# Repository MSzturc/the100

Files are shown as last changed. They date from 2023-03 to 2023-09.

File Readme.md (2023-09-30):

<p>

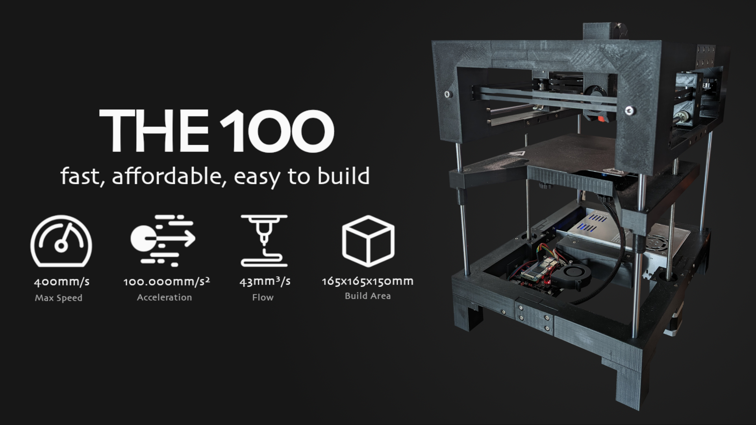
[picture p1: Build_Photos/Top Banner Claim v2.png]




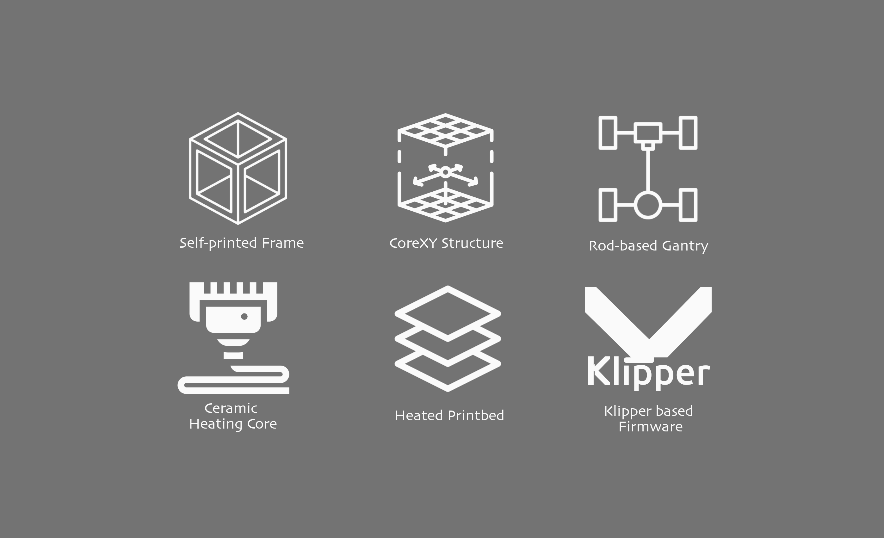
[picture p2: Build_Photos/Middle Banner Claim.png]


<a href="https://www.youtube.com/watch?v=oDKtKg4UfsU" > 
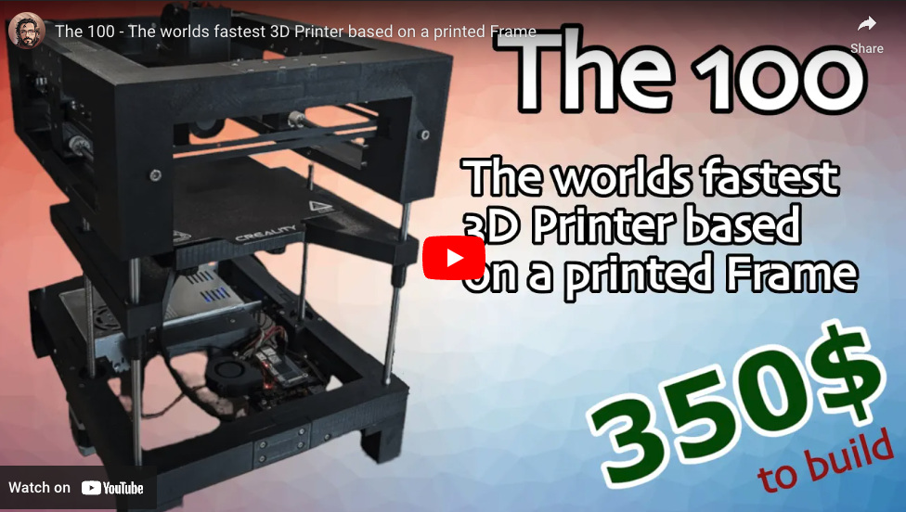
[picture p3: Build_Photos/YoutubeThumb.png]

</a>

</p>

# THE 100, the fastest 3D Printer based on a printed frame.

- It does Speedboat in less than 6 minutes and is capable of doing high quality prints in **1/10th** of the time a Ender 3 would need.
- By the time releasing, The 100 is at the 26th rank of the [leaderboard](https://docs.google.com/spreadsheets/d/1lFiJi-X3Xm3hh3I9Ty9dfACMiBWxHFAOUeiU1km9m6I/edit#gid=106736391) of the fastest printers in the world and it's the fastest one that uses a 3d printed frame.
- And the best thing, this printer **100% open source**. Which means if you like this printer and you  like to build one by own, you find all resources needed to do this in this repository

## Links
- [Bill of Material](https://docs.google.com/spreadsheets/d/1e5dhm4ck-dtci_GDkMuuwxgp788YJ5hdL6JvRKvF1Zc/edit?usp=sharing)
- [Join our Discord Server](https://discord.gg/fW7BcUErgZ)
- [Support this Project on Patreon](https://www.patreon.com/The100)
- [Grad the CAD files](https://www.printables.com/model/572689-the-100-the-fastest-3d-printer-based-on-a-printed-)
- [View the Assembly Guide](https://www.youtube.com/playlist?list=PLM01o_dfwbDcKYB-9yV0vLs5k0CrHUv0W)
- [Follow the Development](https://hackaday.io/project/190348-the-100-the-fastest-3d-printer)
- [Our Community on Facebook](https://www.facebook.com/groups/181335024786568)
- [Printers build by the Community](https://www.youtube.com/playlist?list=PLM01o_dfwbDfZ-m0T0c431_AJRJ2Jxip3)

## Print Settings

To print the STL files, a 3D printer with a print bed of at least 230x230mm is required.
I've printed all parts out of PLA. If you plan to print ABS/ASA on the printer i would suggest to print the print bed out of a more temprature resistant material.

For all STL Parts **exept the print bed** i've used the following settings:

- 0.25 Layer height
- 0.5 Line width
- 3 Top layers
- 3 Bottom layers
- 3 Walls
- 25% Infill
- Grid Infill Pattern

**For the print bed:**
- 30% Infill

The infill of the print bed needs to be slightly higher to move the center of gravity to where the lead screws are attached. This is needed to stop binding on the Z-Axis.

## Specifications

- Printing Technology: FDM
- Build Volume: 165x165x150mm
- Maximum Printing Speed: 400mm/s
- Maximum Acceleration: 100.000mm/s²
- Layer Height: 0.1-0.35mm
- Extruder: BMG Bowden Extruder
- Filament Diameter: 1.75mm
- Nozzle Diameter: 0.4 (swappable)
- Maximum Nozzle Temperature: 300°C
- Maximum Heatbed Temperature: 110°C
- Leveling Mode: manual
- File Transfer: USB Drive, WIFI
- Rated Power: 350W
- Supported Filaments: PLA, PETG

## Builds by the Community

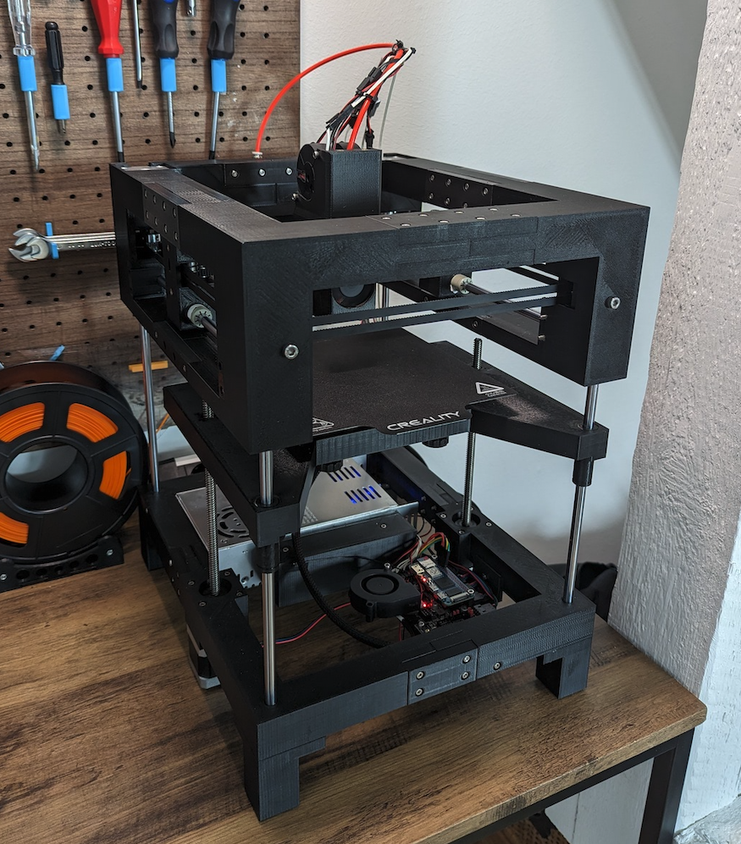
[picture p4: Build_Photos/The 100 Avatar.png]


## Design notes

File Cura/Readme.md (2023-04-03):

1. Add a new Printer in Cura:

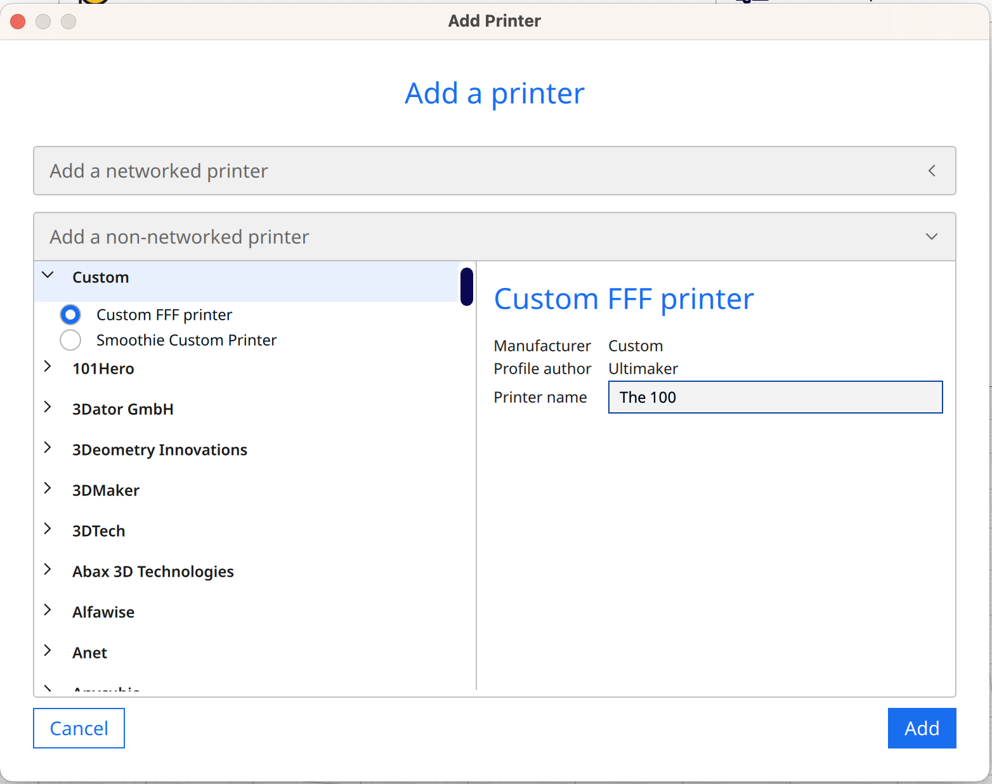
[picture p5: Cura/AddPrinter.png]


2. With following Printer Settings:

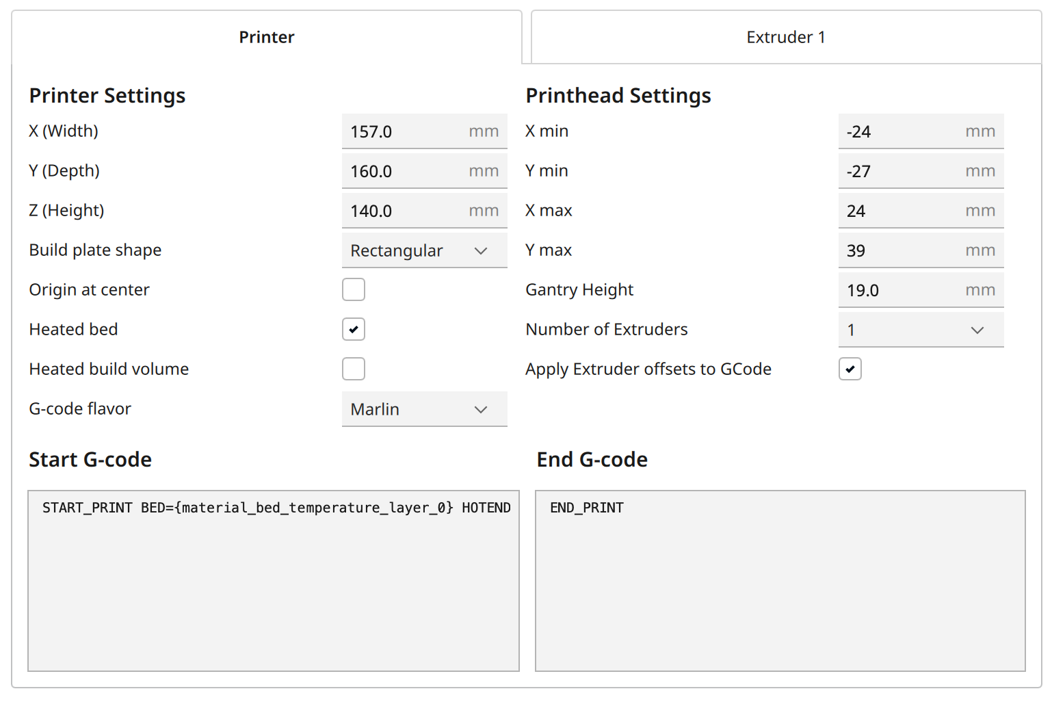
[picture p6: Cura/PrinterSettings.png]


Use as start GCODE:

> START_PRINT BED={material_bed_temperature_layer_0} HOTEND={material_print_temperature_layer_0}

3. and following Extruder Settings:

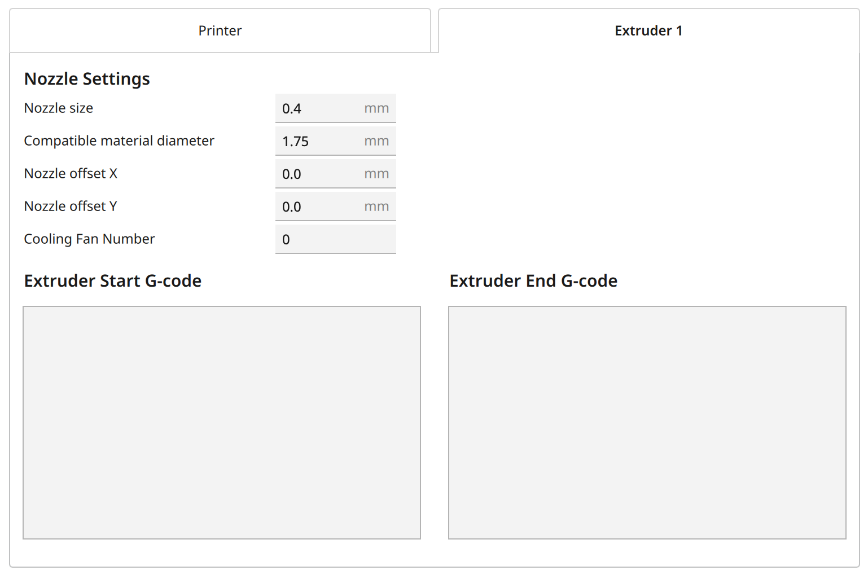
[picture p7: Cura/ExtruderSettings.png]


4. Import profiles at **Preferences->Configure Cura->Profiles** by pressing the Import button
5. Install the Moonraker plugin to communicate with the printer through WIFI. You have to add the Ip Address of the printer in the Moonraker Settings.

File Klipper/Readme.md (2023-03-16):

This config is for the BIGTREETECH SKR Pico.
It uses Klipper v0.11.0.116  with mainsail 2.4.1 and moonraker 0.7.1

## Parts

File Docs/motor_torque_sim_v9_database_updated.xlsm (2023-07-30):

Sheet: UI
 |  |  |  |  |  |  |  |  |  |  |  |  |  |  |  |  | Stepper Torque, 24V, 20T, 20k, 500g, 50W |  |  |  |  |  |  |  |  |  |  |  |  |  |  |  |  | Stepper Power, 24V, 20T, 20k, 500g, 50W
 | Input Voltage | 24 | Volts |  | 24V, 20T, 20k, 500g, 50W |  |  |  |  |  |  |  |  |  |  | mm/s | Cloudray-17CS05A-180E | LDO-42STH48-2504AC | Wantai-42BYGHW811 | G-Penny-42HS4825A4 | RATTM-17HS3410 | LDO-42STH48-2804AC | YunTaiKe-42CM02 | Motech-MT-1704HSM168RE | LDO-42STH48-2504MAC(F) | Moons-MS17HA2P4200 | 0 | 0 | 0 | 0 | 0 | 0 | Torque Required | mm/s | Cloudray-17CS05A-180E | LDO-42STH48-2504AC | Wantai-42BYGHW811 | G-Penny-42HS4825A4 | RATTM-17HS3410 | LDO-42STH48-2804AC | YunTaiKe-42CM02 | Motech-MT-1704HSM168RE | LDO-42STH48-2504MAC(F) | Moons-MS17HA2P4200 | 0 | 0 | 0 | 0 | 0 | 0
 | Max Drive Current | 0.8 | Amps |  |  |  |  |  |  |  |  |  |  |  | 0 | 0 | 13.8 | 9.8 | 8.5 | 9.2 | 8.3 | 5.8 | 6.4 | 12.4 | 7.5 | 9.2 | #VALUE! | #VALUE! | #VALUE! | #VALUE! | #VALUE! | #VALUE! | 6.4 | 0 | 1.5 | 0.8 | 0.8 | 1.0 | 0.8 | 0.4 | 0.9 | 1.1 | 0.8 | 0.7 | #VALUE! | #VALUE! | #VALUE! | #VALUE! | #VALUE! | #VALUE!
 | Max Drive Percent | 100% |  |  |  |  |  |  |  |  |  |  |  |  | 0.5 | 20 | 13.8 | 9.8 | 8.5 | 9.2 | 8.3 | 5.8 | 6.4 | 12.4 | 7.5 | 9.2 | #VALUE! | #VALUE! | #VALUE! | #VALUE! | #VALUE! | #VALUE! | 6.4 | 20 | 2.0 | 1.2 | 1.1 | 1.4 | 1.1 | 0.7 | 1.1 | 1.5 | 1.1 | 1.0 | #VALUE! | #VALUE! | #VALUE! | #VALUE! | #VALUE! | #VALUE!
 | Max Power | 50 | W |  |  |  |  |  |  |  |  |  |  |  | 1 | 40 | 13.8 | 9.8 | 8.5 | 9.2 | 8.3 | 5.8 | 6.4 | 12.4 | 7.5 | 9.2 | #VALUE! | #VALUE! | #VALUE! | #VALUE! | #VALUE! | #VALUE! | 6.4 | 40 | 2.6 | 1.6 | 1.5 | 1.7 | 1.4 | 1.0 | 1.4 | 2.0 | 1.4 | 1.4 | #VALUE! | #VALUE! | #VALUE! | #VALUE! | #VALUE! | #VALUE!
 | Pulley Size | 20 | Teeth | 6.366197724 | mm |  |  |  |  |  |  |  |  |  | 1.5 | 60 | 13.8 | 9.8 | 8.5 | 9.2 | 8.3 | 5.8 | 6.4 | 12.4 | 7.5 | 9.2 | #VALUE! | #VALUE! | #VALUE! | #VALUE! | #VALUE! | #VALUE! | 6.4 | 60 | 3.1 | 1.9 | 1.8 | 2.1 | 1.6 | 1.2 | 1.6 | 2.4 | 1.7 | 1.7 | #VALUE! | #VALUE! | #VALUE! | #VALUE! | #VALUE! | #VALUE!
 | Gear Ratio | 1 |  |  |  |  |  |  |  |  |  |  |  |  | 2 | 80 | 13.8 | 9.8 | 8.5 | 9.2 | 8.3 | 5.8 | 6.4 | 12.4 | 7.5 | 9.2 | #VALUE! | #VALUE! | #VALUE! | #VALUE! | #VALUE! | #VALUE! | 6.4 | 80 | 3.6 | 2.3 | 2.1 | 2.4 | 1.9 | 1.5 | 1.8 | 2.9 | 2.0 | 2.1 | #VALUE! | #VALUE! | #VALUE! | #VALUE! | #VALUE! | #VALUE!
 |  |  |  |  |  |  |  |  |  |  |  |  |  |  | 2.5 | 100 | 13.8 | 9.8 | 8.5 | 9.2 | 8.3 | 5.8 | 6.4 | 12.4 | 7.5 | 9.2 | #VALUE! | #VALUE! | #VALUE! | #VALUE! | #VALUE! | #VALUE! | 6.4 | 100 | 4.1 | 2.7 | 2.5 | 2.8 | 2.2 | 1.8 | 2.1 | 3.3 | 2.4 | 2.4 | #VALUE! | #VALUE! | #VALUE! | #VALUE! | #VALUE! | #VALUE!
 | Acceleration | 20000 | mm/s^2 |  |  |  |  |  |  |  |  |  |  |  | 3 | 120 | 13.8 | 9.8 | 8.5 | 9.2 | 8.3 | 5.8 | 6.4 | 12.4 | 7.5 | 9.2 | #VALUE! | #VALUE! | #VALUE! | #VALUE! | #VALUE! | #VALUE! | 6.4 | 120 | 4.6 | 3.1 | 2.8 | 3.2 | 2.5 | 2.0 | 2.3 | 3.8 | 2.7 | 2.8 | #VALUE! | #VALUE! | #VALUE! | #VALUE! | #VALUE! | #VALUE!
 | Toolhead + Y axis mass | 500 | g |  |  |  |  |  |  |  |  |  |  |  | 3.5 | 140 | 13.8 | 9.8 | 8.5 | 9.2 | 8.3 | 5.8 | 6.4 | 12.4 | 7.5 | 9.2 | #VALUE! | #VALUE! | #VALUE! | #VALUE! | #VALUE! | #VALUE! | 6.4 | 140 | 5.1 | 3.5 | 3.1 | 3.5 | 2.8 | 2.3 | 2.6 | 4.2 | 3.0 | 3.1 | #VALUE! | #VALUE! | #VALUE! | #VALUE! | #VALUE! | #VALUE!
 | Torque Required | 6.37 | N-cm | 0.06366197724 |  |  |  |  |  |  |  |  |  |  | 4 | 160 | 13.8 | 9.8 | 8.5 | 9.2 | 8.3 | 5.8 | 6.4 | 12.4 | 7.5 | 9.2 | #VALUE! | #VALUE! | #VALUE! | #VALUE! | #VALUE! | #VALUE! | 6.4 | 160 | 5.6 | 3.9 | 3.5 | 3.9 | 3.1 | 2.6 | 2.8 | 4.7 | 3.3 | 3.4 | #VALUE! | #VALUE! | #VALUE! | #VALUE! | #VALUE! | #VALUE!
 |  |  |  |  |  |  |  |  |  |  |  |  |  |  | 4.5 | 180 | 13.8 | 9.8 | 8.5 | 9.2 | 8.3 | 5.8 | 6.4 | 12.4 | 7.5 | 9.2 | #VALUE! | #VALUE! | #VALUE! | #VALUE! | #VALUE! | #VALUE! | 6.4 | 180 | 6.2 | 4.3 | 3.8 | 4.2 | 3.4 | 2.8 | 3.0 | 5.2 | 3.6 | 3.8 | #VALUE! | #VALUE! | #VALUE! | #VALUE! | #VALUE! | #VALUE!
 |  |  | NEMA | Body Length | Step Angle | Rated Current | Torque | Inductance | Resistance | Rotor Inertia | Max Current at Specified Power | Drive Current | Torque Rotor | Power at drive current | 5 | 200 | 13.8 | 9.8 | 8.5 | 9.2 | 8.3 | 5.8 | 6.4 | 12.4 | 7.5 | 9.2 | #VALUE! | #VALUE! | #VALUE! | #VALUE! | #VALUE! | #VALUE! | 6.4 | 200 | 6.7 | 4.7 | 4.1 | 4.6 | 3.7 | 3.1 | 3.3 | 5.6 | 4.0 | 4.1 | #VALUE! | #VALUE! | #VALUE! | #VALUE! | #VALUE! | #VALUE!
Motor 1 |  | Cloudray-17CS05A-180E | 17 | 48 | 1.8 | 1.8 | 52 | 5.8 | 2.4 | 82 | 3.23 | 0.80 | 2.58 | 3.072 | 5.5 | 220 | 13.8 | 9.8 | 8.5 | 9.2 | 8.3 | 5.8 | 6.4 | 12.4 | 7.5 | 9.2 | #VALUE! | #VALUE! | #VALUE! | #VALUE! | #VALUE! | #VALUE! | 6.4 | 220 | 7.2 | 5.1 | 4.5 | 4.9 | 4.0 | 3.4 | 3.5 | 6.1 | 4.3 | 4.5 | #VALUE! | #VALUE! | #VALUE! | #VALUE! | #VALUE! | #VALUE!
Motor 2 |  | LDO-42STH48-2504AC | 17 | 48 | 1.8 | 2.5 | 55 | 1.5 | 1.2 | 84.5 | 4.56 | 0.80 | 2.65 | 1.536 | 6 | 240 | 13.8 | 9.8 | 8.5 | 9.2 | 8.3 | 5.8 | 6.4 | 12.4 | 7.5 | 9.2 | #VALUE! | #VALUE! | #VALUE! | #VALUE! | #VALUE! | #VALUE! | 6.4 | 240 | 7.7 | 5.5 | 4.8 | 5.3 | 4.3 | 3.6 | 3.7 | 6.5 | 4.6 | 4.8 | #VALUE! | #VALUE! | #VALUE! | #VALUE! | #VALUE! | #VALUE!
Motor 3 |  | Wantai-42BYGHW811 | 17 | 48 | 1.8 | 2.5 | 47 | 1.8 | 1.25 | 68 | 4.47 | 0.80 | 2.14 | 1.6 | 6.5 | 260 | 13.8 | 9.8 | 8.5 | 9.2 | 8.3 | 5.8 | 6.4 | 12.4 | 7.5 | 9.2 | #VALUE! | #VALUE! | #VALUE! | #VALUE! | #VALUE! | #VALUE! | 6.4 | 260 | 8.2 | 5.9 | 5.1 | 5.6 | 4.6 | 3.9 | 4.0 | 7.0 | 4.9 | 5.2 | #VALUE! | #VALUE! | #VALUE! | #VALUE! | #VALUE! | #VALUE!
Motor 4 |  | G-Penny-42HS4825A4 | 17 | 48 | 1.8 | 2.5 | 50 | 1.8 | 1.6 | 68 | 3.95 | 0.80 | 2.14 | 2.048 | 7 | 280 | 13.8 | 9.8 | 8.5 | 9.2 | 8.3 | 5.8 | 6.4 | 12.4 | 7.5 | 9.2 | #VALUE! | #VALUE! | #VALUE! | #VALUE! | #VALUE! | #VALUE! | 6.4 | 280 | 8.7 | 6.2 | 5.5 | 6.0 | 4.9 | 4.2 | 4.2 | 7.4 | 5.2 | 5.5 | #VALUE! | #VALUE! | #VALUE! | #VALUE! | #VALUE! | #VALUE!
Motor 5 |  | RATTM-17HS3410 | 17 | 34 | 1.8 | 1.7 | 28 | 1.8 | 1.2 | 34 | 4.56 | 0.80 | 1.07 | 1.536 | 7.5 | 300 | 13.8 | 9.8 | 8.5 | 9.2 | 8.3 | 5.8 | 6.4 | 12.4 | 7.5 | 9.2 | #VALUE! | #VALUE! | #VALUE! | #VALUE! | #VALUE! | #VALUE! | 6.4 | 300 | 9.2 | 6.6 | 5.8 | 6.4 | 5.2 | 4.4 | 4.5 | 7.9 | 5.6 | 5.9 | #VALUE! | #VALUE! | #VALUE! | #VALUE! | #VALUE! | #VALUE!
Motor 6 |  | LDO-42STH48-2804AC | 17 | 48 | 1.8 | 2.8 | 42 | 0.6 | 0.7 | 84.5 | 5.98 | 0.80 | 2.65 | 0.896 | 8 | 320 | 13.8 | 9.8 | 8.5 | 9.2 | 8.3 | 5.8 | 6.4 | 12.4 | 7.5 | 9.2 | #VALUE! | #VALUE! | #VALUE! | #VALUE! | #VALUE! | #VALUE! | 6.4 | 320 | 9.8 | 7.0 | 6.1 | 6.7 | 5.5 | 4.7 | 4.7 | 8.4 | 5.9 | 6.2 | #VALUE! | #VALUE! | #VALUE! | #VALUE! | #VALUE! | #VALUE!
Motor 7 |  | YunTaiKe-42CM02 | 17 | 33 | 1.8 | 1.5 | 20 | 1.4 | 1.4 | 35 | 4.23 | 0.80 | 1.10 | 1.792 | 8.5 | 340 | 12.4 | 9.8 | 8.5 | 9.2 | 8.3 | 5.8 | 6.4 | 12.4 | 7.5 | 9.2 | #VALUE! | #VALUE! | #VALUE! | #VALUE! | #VALUE! | #VALUE! | 6.4 | 340 | 9.3 | 7.4 | 6.5 | 7.1 | 5.7 | 5.0 | 4.9 | 8.8 | 6.2 | 6.6 | #VALUE! | #VALUE! | #VALUE! | #VALUE! | #VALUE! | #VALUE!
Motor 8 |  | Motech-MT-1704HSM168RE | 17 | 48 | 0.9 | 1.68 | 43.12 | 2.8 | 1.65 | 68 | 3.89 | 0.80 | 2.14 |  | 9 | 360 | 11.0 | 9.8 | 8.5 | 9.2 | 8.3 | 5.8 | 6.4 | 12.1 | 7.5 | 9.2 | #VALUE! | #VALUE! | #VALUE! | #VALUE! | #VALUE! | #VALUE! | 6.4 | 360 | 8.7 | 7.8 | 6.8 | 7.4 | 6.0 | 5.2 | 5.2 | 9.1 | 6.5 | 6.9 | #VALUE! | #VALUE! | #VALUE! | #VALUE! | #VALUE! | #VALUE!
Motor 9 |  | LDO-42STH48-2504MAC(F) | 17 | 48 | 0.9 | 2.5 | 45 | 1.5 | 1.2 | 85 | 4.56 | 0.80 | 2.67 |  | 9.5 | 380 | 9.7 | 9.8 | 8.5 | 9.2 | 8.3 | 5.8 | 6.4 | 10.9 | 7.5 | 9.2 | #VALUE! | #VALUE! | #VALUE! | #VALUE! | #VALUE! | #VALUE! | 6.4 | 380 | 8.2 | 8.2 | 7.1 | 7.8 | 6.3 | 5.5 | 5.4 | 8.6 | 6.8 | 7.3 | #VALUE! | #VALUE! | #VALUE! | #VALUE! | #VALUE! | #VALUE!
Motor 10 |  | Moons-MS17HA2P4200 | 17 | 40 | 0.9 | 2 | 39 | 2.8 | 1.05 | 57 | 4.88 | 0.80 | 1.79 |  | 10 | 400 | 8.5 | 9.8 | 8.5 | 9.2 | 8.3 | 5.8 | 6.4 | 9.7 | 7.5 | 9.2 | #VALUE! | #VALUE! | #VALUE! | #VALUE! | #VALUE! | #VALUE! | 6.4 | 400 | 7.7 | 8.6 | 7.5 | 8.1 | 6.6 | 5.8 | 5.6 | 8.2 | 7.2 | 7.6 | #VALUE! | #VALUE! | #VALUE! | #VALUE! | #VALUE! | #VALUE!
Motor 11 |  |  | #N/A | #N/A | #N/A | #N/A | #N/A | #N/A | #N/A | #N/A | #N/A | #N/A | #N/A |  | 10.5 | 420 | 7.4 | 9.8 | 8.5 | 9.2 | 8.3 | 5.8 | 6.4 | 8.7 | 7.5 | 8.7 | #VALUE! | #VALUE! | #VALUE! | #VALUE! | #VALUE! | #VALUE! | 6.4 | 420 | 7.2 | 9.0 | 7.8 | 8.5 | 6.9 | 6.0 | 5.9 | 7.7 | 7.5 | 7.6 | #VALUE! | #VALUE! | #VALUE! | #VALUE! | #VALUE! | #VALUE!
Motor 12 |  |  | #N/A | #N/A | #N/A | #N/A | #N/A | #N/A | #N/A | #N/A | #N/A | #N/A | #N/A |  | 11 | 440 | 6.4 | 9.8 | 8.5 | 9.2 | 8.3 | 5.8 | 6.4 | 7.8 | 7.5 | 8.0 | #VALUE! | #VALUE! | #VALUE! | #VALUE! | #VALUE! | #VALUE! | 6.4 | 440 | 6.7 | 9.4 | 8.2 | 8.8 | 7.2 | 6.3 | 6.1 | 7.3 | 7.8 | 7.3 | #VALUE! | #VALUE! | #VALUE! | #VALUE! | #VALUE! | #VALUE!
Motor 13 |  |  | #N/A | #N/A | #N/A | #N/A | #N/A | #N/A | #N/A | #N/A | #N/A | #N/A | #N/A |  | 11.5 | 460 | 5.5 | 9.8 | 8.5 | 9.2 | 8.3 | 5.8 | 6.4 | 6.9 | 7.5 | 7.3 | #VALUE! | #VALUE! | #VALUE! | #VALUE! | #VALUE! | #VALUE! | 6.4 | 460 | 6.2 | 9.8 | 8.5 | 9.2 | 7.5 | 6.6 | 6.3 | 6.9 | 8.1 | 7.0 | #VALUE! | #VALUE! | #VALUE! | #VALUE! | #VALUE! | #VALUE!
Motor 14 |  |  | #N/A | #N/A | #N/A | #N/A | #N/A | #N/A | #N/A | #N/A | #N/A | #N/A | #N/A |  | 12 | 480 | 4.7 | 9.8 | 8.5 | 9.2 | 8.3 | 5.8 | 6.4 | 6.1 | 7.5 | 6.7 | #VALUE! | #VALUE! | #VALUE! | #VALUE! | #VALUE! | #VALUE! | 6.4 | 480 | 5.8 | 10.2 | 8.8 | 9.6 | 7.8 | 6.8 | 6.6 | 6.5 | 8.4 | 6.8 | #VALUE! | #VALUE! | #VALUE! | #VALUE! | #VALUE! | #VALUE!
Motor 15 |  |  | #N/A | #N/A | #N/A | #N/A | #N/A | #N/A | #N/A | #N/A | #N/A | #N/A | #N/A |  | 12.5 | 500 | 3.9 | 9.8 | 8.5 | 9.2 | 8.3 | 5.8 | 6.4 | 5.3 | 7.5 | 6.1 | #VALUE! | #VALUE! | #VALUE! | #VALUE! | #VALUE! | #VALUE! | 6.4 | 500 | 5.3 | 10.5 | 9.2 | 9.9 | 8.1 | 7.1 | 6.8 | 6.2 | 8.8 | 6.5 | #VALUE! | #VALUE! | #VALUE! | #VALUE! | #VALUE! | #VALUE!
Motor 16 |  |  | #N/A | #N/A | #N/A | #N/A | #N/A | #N/A | #N/A | #N/A | #N/A | #N/A | #N/A |  | 13 | 520 | 3.2 | 9.8 | 8.5 | 9.2 | 8.3 | 5.8 | 6.4 | 4.7 | 7.5 | 5.6 | #VALUE! | #VALUE! | #VALUE! | #VALUE! | #VALUE! | #VALUE! | 6.4 | 520 | 4.9 | 10.9 | 9.5 | 10.3 | 8.4 | 7.4 | 7.1 | 5.8 | 9.1 | 6.3 | #VALUE! | #VALUE! | #VALUE! | #VALUE! | #VALUE! | #VALUE!
 |  |  |  |  |  |  |  |  |  |  |  |  |  |  | 13.5 | 540 | 2.5 | 9.8 | 8.5 | 9.2 | 8.3 | 5.8 | 6.4 | 4.0 | 7.5 | 5.1 | #VALUE! | #VALUE! | #VALUE! | #VALUE! | #VALUE! | #VALUE! | 6.4 | 540 | 4.4 | 11.3 | 9.8 | 10.6 | 8.7 | 7.6 | 7.3 | 5.4 | 9.4 | 6.1 | #VALUE! | #VALUE! | #VALUE! | #VALUE! | #VALUE! | #VALUE!
 |  |  |  |  |  |  |  |  |  |  |  |  |  |  | 14 | 560 | 1.8 | 9.8 | 8.5 | 9.2 | 8.3 | 5.8 | 6.4 | 3.4 | 7.5 | 4.6 | #VALUE! | #VALUE! | #VALUE! | #VALUE! | #VALUE! | #VALUE! | 6.4 | 560 | 4.0 | 11.7 | 10.2 | 11.0 | 9.0 | 7.9 | 7.5 | 5.0 | 9.7 | 5.8 | #VALUE! | #VALUE! | #VALUE! | #VALUE! | #VALUE! | #VALUE!
 |  |  |  |  |  |  |  |  |  |  |  |  |  |  | 14.5 | 580 | 1.2 | 9.8 | 8.5 | 9.2 | 8.3 | 5.8 | 6.4 | 2.9 | 7.5 | 4.1 | #VALUE! | #VALUE! | #VALUE! | #VALUE! | #VALUE! | #VALUE! | 6.4 | 580 | 3.6 | 12.1 | 10.5 | 11.3 | 9.3 | 8.2 | 7.8 | 4.7 | 10.0 | 5.6 | #VALUE! | #VALUE! | #VALUE! | #VALUE! | #VALUE! | #VALUE!
 |  |  |  |  |  |  |  |  |  |  |  |  |  |  | 15 | 600 | 0.7 | 9.8 | 8.5 | 9.2 | 8.3 | 5.8 | 6.4 | 2.3 | 7.3 | 3.7 | #VALUE! | #VALUE! | #VALUE! | #VALUE! | #VALUE! | #VALUE! | 6.4 | 600 | 3.1 | 12.5 | 10.8 | 11.7 | 9.6 | 8.4 | 8.0 | 4.3 | 10.1 | 5.4 | #VALUE! | #VALUE! | #VALUE! | #VALUE! | #VALUE! | #VALUE!
 |  |  |  |  |  |  |  |  |  |  |  |  |  |  | 15.5 | 620 | 0.2 | 9.8 | 8.5 | 9.2 | 8.3 | 5.8 | 6.4 | 1.8 | 6.7 | 3.4 | #VALUE! | #VALUE! | #VALUE! | #VALUE! | #VALUE! | #VALUE! | 6.4 | 620 | 2.7 | 12.9 | 11.2 | 12.0 | 9.8 | 8.7 | 8.2 | 3.9 | 9.7 | 5.2 | #VALUE! | #VALUE! | #VALUE! | #VALUE! | #VALUE! | #VALUE!
 |  |  |  |  |  |  |  |  |  |  |  |  |  |  | 16 | 640 | -0.3 | 9.8 | 8.5 | 9.2 | 8.3 | 5.8 | 6.4 | 1.4 | 6.1 | 3.0 | #VALUE! | #VALUE! | #VALUE! | #VALUE! | #VALUE! | #VALUE! | 6.4 | 640 | 2.3 | 13.3 | 11.5 | 12.4 | 10.1 | 9.0 | 8.5 | 3.6 | 9.4 | 4.9 | #VALUE! | #VALUE! | #VALUE! | #VALUE! | #VALUE! | #VALUE!
 |  |  |  |  |  |  |  |  |  |  |  |  |  |  | 16.5 | 660 | -0.8 | 9.8 | 8.5 | 9.2 | 8.3 | 5.8 | 6.4 | 0.9 | 5.5 | 2.7 | #VALUE! | #VALUE! | #VALUE! | #VALUE! | #VALUE! | #VALUE! | 6.4 | 660 | 1.9 | 13.7 | 11.8 | 12.8 | 10.4 | 9.2 | 8.7 | 3.2 | 9.0 | 4.7 | #VALUE! | #VALUE! | #VALUE! | #VALUE! | #VALUE! | #VALUE!
 |  |  |  |  |  |  |  |  |  |  |  |  |  |  | 17 | 680 | -1.2 | 9.8 | 8.5 | 9.1 | 8.3 | 5.8 | 6.4 | 0.5 | 5.0 | 2.3 | #VALUE! | #VALUE! | #VALUE! | #VALUE! | #VALUE! | #VALUE! | 6.4 | 680 | 1.4 | 14.1 | 12.2 | 13.0 | 10.7 | 9.5 | 9.0 | 2.9 | 8.7 | 4.5 | #VALUE! | #VALUE! | #VALUE! | #VALUE! | #VALUE! | #VALUE!
 |  |  |  |  |  |  |  |  |  |  |  |  |  |  | 17.5 | 700 | -1.7 | 8.7 | 8.5 | 8.3 | 8.3 | 5.8 | 6.4 | 0.1 | 4.5 | 2.0 | #VALUE! | #VALUE! | #VALUE! | #VALUE! | #VALUE! | #VALUE! | 6.4 | 700 | 1.0 | 13.1 | 12.5 | 12.3 | 11.0 | 9.8 | 9.2 | 2.5 | 8.3 | 4.3 | #VALUE! | #VALUE! | #VALUE! | #VALUE! | #VALUE! | #VALUE!
 |  |  |  |  |  |  |  |  |  |  |  |  |  |  | 18 | 720 | -2.1 | 7.6 | 8.3 | 7.5 | 8.3 | 5.8 | 6.4 | -0.2 | 4.1 | 1.8 | #VALUE! | #VALUE! | #VALUE! | #VALUE! | #VALUE! | #VALUE! | 6.4 | 720 | 0.6 | 12.2 | 12.6 | 11.6 | 11.3 | 10.0 | 9.4 | 2.2 | 7.9 | 4.1 | #VALUE! | #VALUE! | #VALUE! | #VALUE! | #VALUE! | #VALUE!
 |  |  |  |  |  |  |  |  |  |  |  |  |  |  | 18.5 | 740 | -2.4 | 6.6 | 7.6 | 6.7 | 8.3 | 5.8 | 6.4 | -0.6 | 3.6 | 1.5 | #VALUE! | #VALUE! | #VALUE! | #VALUE! | #VALUE! | #VALUE! | 6.4 | 740 | 0.2 | 11.2 | 11.9 | 10.9 | 11.6 | 10.3 | 9.7 | 1.8 | 7.6 | 3.9 | #VALUE! | #VALUE! | #VALUE! | #VALUE! | #VALUE! | #VALUE!
 |  |  |  |  |  |  |  |  |  |  |  |  |  |  | 19 | 760 | -2.6 | 5.7 | 6.9 | 6.0 | 8.3 | 5.8 | 6.4 | -0.9 | 3.2 | 1.2 | #VALUE! | #VALUE! | #VALUE! | #VALUE! | #VALUE! | #VALUE! | 6.4 | 760 | 0.0 | 10.3 | 11.3 | 10.3 | 11.9 | 10.6 | 9.9 | 1.4 | 7.3 | 3.6 | #VALUE! | #VALUE! | #VALUE! | #VALUE! | #VALUE! | #VALUE!
 |  |  |  |  |  |  |  |  |  |  |  |  |  |  | 19.5 | 780 | -2.6 | 4.7 | 6.2 | 5.3 | 8.2 | 5.8 | 6.4 | -1.2 | 2.8 | 1.0 | #VALUE! | #VALUE! | #VALUE! | #VALUE! | #VALUE! | #VALUE! | 6.4 | 780 | 0.0 | 9.3 | 10.7 | 9.6 | 12.1 | 10.8 | 10.1 | 1.1 | 6.9 | 3.4 | #VALUE! | #VALUE! | #VALUE! | #VALUE! | #VALUE! | #VALUE!
 |  |  |  |  |  |  |  |  |  |  |  |  |  |  | 20 | 800 | -2.6 | 3.9 | 5.6 | 4.7 | 7.7 | 5.8 | 6.4 | -1.5 | 2.4 | 0.7 | #VALUE! | #VALUE! | #VALUE! | #VALUE! | #VALUE! | #VALUE! | 6.4 | 800 | 0.0 | 8.4 | 10.1 | 8.9 | 11.6 | 11.1 | 10.4 | 0.7 | 6.6 | 3.2 | #VALUE! | #VALUE! | #VALUE! | #VALUE! | #VALUE! | #VALUE!
 |  |  |  |  |  |  |  |  |  |  |  |  |  |  | 20.5 | 820 | -2.6 | 3.0 | 5.0 | 4.1 | 7.1 | 5.8 | 6.4 | -1.8 | 2.0 | 0.5 | #VALUE! | #VALUE! | #VALUE! | #VALUE! | #VALUE! | #VALUE! | 6.4 | 820 | 0.0 | 7.5 | 9.5 | 8.3 | 11.1 | 11.4 | 10.6 | 0.4 | 6.2 | 3.0 | #VALUE! | #VALUE! | #VALUE! | #VALUE! | #VALUE! | #VALUE!
 |  |  |  |  |  |  |  |  |  |  |  |  |  |  | 21 | 840 | -2.6 | 2.2 | 4.4 | 3.5 | 6.6 | 5.8 | 6.4 | -2.1 | 1.7 | 0.3 | #VALUE! | #VALUE! | #VALUE! | #VALUE! | #VALUE! | #VALUE! | 6.4 | 840 | 0.0 | 6.5 | 8.9 | 7.6 | 10.7 | 11.6 | 10.8 | 0.03100021401 | 5.9 | 2.8 | #VALUE! | #VALUE! | #VALUE! | #VALUE! | #VALUE! | #VALUE!
 |  |  |  |  |  |  |  |  |  |  |  |  |  |  | 21.5 | 860 | -2.6 | 1.4 | 3.9 | 2.9 | 6.1 | 5.8 | 6.4 | -2.1 | 1.4 | 0.1 | #VALUE! | #VALUE! | #VALUE! | #VALUE! | #VALUE! | #VALUE! | 6.4 | 860 | 0.0 | 5.6 | 8.3 | 7.0 | 10.2 | 11.9 | 11.1 | 0.0 | 5.6 | 2.6 | #VALUE! | #VALUE! | #VALUE! | #VALUE! | #VALUE! | #VALUE!
 |  |  |  |  |  |  |  |  |  |  |  |  |  |  | 22 | 880 | -2.6 | 0.7 | 3.3 | 2.3 | 5.7 | 5.8 | 6.4 | -2.1 | 1.0 | -0.1 | #VALUE! | #VALUE! | #VALUE! | #VALUE! | #VALUE! | #VALUE! | 6.4 | 880 | 0.0 | 4.7 | 7.8 | 6.4 | 9.7 | 12.2 | 11.3 | 0.0 | 5.2 | 2.4 | #VALUE! | #VALUE! | #VALUE! | #VALUE! | #VALUE! | #VALUE!
 |  |  |  |  |  |  |  |  |  |  |  |  |  |  | 22.5 | 900 | -2.6 | -0.01148493518 | 2.8 | 1.8 | 5.2 | 5.8 | 6.4 | -2.1 | 0.7 | -0.3 | #VALUE! | #VALUE! | #VALUE! | #VALUE! | #VALUE! | #VALUE! | 6.4 | 900 | 0.0 | 3.8 | 7.2 | 5.7 | 9.3 | 12.4 | 11.6 | 0.0 | 4.9 | 2.2 | #VALUE! | #VALUE! | #VALUE! | #VALUE! | #VALUE! | #VALUE!
 |  |  |  |  |  |  |  |  |  |  |  |  |  |  | 23 | 920 | -2.6 | -0.7 | 2.3 | 1.3 | 4.8 | 5.8 | 6.4 | -2.1 | 0.4 | -0.4 | #VALUE! | #VALUE! | #VALUE! | #VALUE! | #VALUE! | #VALUE! | 6.4 | 920 | 0.0 | 2.9 | 6.6 | 5.1 | 8.8 | 12.7 | 11.8 | 0.0 | 4.6 | 2.0 | #VALUE! | #VALUE! | #VALUE! | #VALUE! | #VALUE! | #VALUE!
 |  |  |  |  |  |  |  |  |  |  |  |  |  |  | 23.5 | 940 | -2.6 | -1.4 | 1.9 | 0.8 | 4.4 | 5.8 | 6.4 | -2.1 | 0.2 | -0.6 | #VALUE! | #VALUE! | #VALUE! | #VALUE! | #VALUE! | #VALUE! | 6.4 | 940 | 0.0 | 1.9 | 6.0 | 4.4 | 8.3 | 13.0 | 12.0 | 0.0 | 4.2 | 1.8 | #VALUE! | #VALUE! | #VALUE! | #VALUE! | #VALUE! | #VALUE!
 |  |  |  |  |  |  |  |  |  |  |  |  |  |  | 24 | 960 | -2.6 | -2.0 | 1.4 | 0.4 | 4.0 | 5.8 | 6.4 | -2.1 | -0.1 | -0.8 | #VALUE! | #VALUE! | #VALUE! | #VALUE! | #VALUE! | #VALUE! | 6.4 | 960 | 0.0 | 1.0 | 5.4 | 3.8 | 7.9 | 13.2 | 12.3 | 0.0 | 3.9 | 1.5 | #VALUE! | #VALUE! | #VALUE! | #VALUE! | #VALUE! | #VALUE!
 |  |  |  |  |  |  |  |  |  |  |  |  |  |  | 24.5 | 980 | -2.6 | -2.6 | 1.0 | -0.1 | 3.6 | 5.8 | 6.2 | -2.1 | -0.4 | -0.9 | #VALUE! | #VALUE! | #VALUE! | #VALUE! | #VALUE! | #VALUE! | 6.4 | 980 | 0.0 | 0.1 | 4.9 | 3.2 | 7.4 | 13.5 | 12.2 | 0.0 | 3.6 | 1.3 | #VALUE! | #VALUE! | #VALUE! | #VALUE! | #VALUE! | #VALUE!
 |  |  |  |  |  |  |  |  |  |  |  |  |  |  | 25 | 1000 | -2.6 | -2.7 | 0.6 | -0.5 | 3.3 | 5.8 | 5.9 | -2.1 | -0.6 | -1.1 | #VALUE! | #VALUE! | #VALUE! | #VALUE! | #VALUE! | #VALUE! | 6.4 | 1000 | 0.0 | 0.0 | 4.3 | 2.5 | 7.0 | 13.8 | 11.7 | 0.0 | 3.3 | 1.1 | #VALUE! | #VALUE! | #VALUE! | #VALUE! | #VALUE! | #VALUE!
 |  |  |  |  |  |  |  |  |  |  |  |  |  |  | 25.5 | 1020 | -2.6 | -2.7 | 0.2 | -1.0 | 2.9 | 5.8 | 5.5 | -2.1 | -0.9 | -1.2 | #VALUE! | #VALUE! | #VALUE! | #VALUE! | #VALUE! | #VALUE! | 6.4 | 1020 | 0.0 | 0.0 | 3.7 | 1.9 | 6.5 | 14.0 | 11.3 | 0.0 | 2.9 | 0.9 | #VALUE! | #VALUE! | #VALUE! | #VALUE! | #VALUE! | #VALUE!
 |  |  |  |  |  |  |  |  |  |  |  |  |  |  | 26 | 1040 | -2.6 | -2.7 | -0.2 | -1.4 | 2.6 | 5.8 | 5.2 | -2.1 | -1.1 | -1.4 | #VALUE! | #VALUE! | #VALUE! | #VALUE! | #VALUE! | #VALUE! | 6.4 | 1040 | 0.0 | 0.0 | 3.1 | 1.3 | 6.1 | 14.3 | 10.9 | 0.0 | 2.6 | 0.7 | #VALUE! | #VALUE! | #VALUE! | #VALUE! | #VALUE! | #VALUE!
 |  |  |  |  |  |  |  |  |  |  |  |  |  |  | 26.5 | 1060 | -2.6 | -2.7 | -0.6 | -1.8 | 2.2 | 5.8 | 4.9 | -2.1 | -1.3 | -1.5 | #VALUE! | #VALUE! | #VALUE! | #VALUE! | #VALUE! | #VALUE! | 6.4 | 1060 | 0.0 | 0.0 | 2.6 | 0.6 | 5.6 | 14.6 | 10.5 | 0.0 | 2.3 | 0.5 | #VALUE! | #VALUE! | #VALUE! | #VALUE! | #VALUE! | #VALUE!
 |  |  |  |  |  |  |  |  |  |  |  |  |  |  | 27 | 1080 | -2.6 | -2.7 | -1.0 | -2.1 | 1.9 | 5.8 | 4.6 | -2.1 | -1.5 | -1.6 | #VALUE! | #VALUE! | #VALUE! | #VALUE! | #VALUE! | #VALUE! | 6.4 | 1080 | 0.0 | 0.0 | 2.0 | 0.007847123056 | 5.2 | 14.8 | 10.2 | 0.0 | 2.0 | 0.3 | #VALUE! | #VALUE! | #VALUE! | #VALUE! | #VALUE! | #VALUE!
 |  |  |  |  |  |  |  |  |  |  |  |  |  |  | 27.5 | 1100 | -2.6 | -2.7 | -1.3 | -2.1 | 1.6 | 5.8 | 4.3 | -2.1 | -1.7 | -1.7 | #VALUE! | #VALUE! | #VALUE! | #VALUE! | #VALUE! | #VALUE! | 6.4 | 1100 | 0.0 | 0.0 | 1.4 | 0.0 | 4.7 | 15.1 | 9.8 | 0.0 | 1.6 | 0.1 | #VALUE! | #VALUE! | #VALUE! | #VALUE! | #VALUE! | #VALUE!
 |  |  |  |  |  |  |  |  |  |  |  |  |  |  | 28 | 1120 | -2.6 | -2.7 | -1.7 | -2.1 | 1.3 | 5.8 | 4.0 | -2.1 | -1.9 | -1.8 | #VALUE! | #VALUE! | #VALUE! | #VALUE! | #VALUE! | #VALUE! | 6.4 | 1120 | 0.0 | 0.0 | 0.8 | 0.0 | 4.3 | 15.4 | 9.4 | 0.0 | 1.3 | 0.0 | #VALUE! | #VALUE! | #VALUE! | #VALUE! | #VALUE! | #VALUE!
 |  |  |  |  |  |  |  |  |  |  |  |  |  |  | 28.5 | 1140 | -2.6 | -2.7 | -2.0 | -2.1 | 1.0 | 5.8 | 3.7 | -2.1 | -2.1 | -1.8 | #VALUE! | #VALUE! | #VALUE! | #VALUE! | #VALUE! | #VALUE! | 6.4 | 1140 | 0.0 | 0.0 | 0.3 | 0.0 | 3.8 | 15.6 | 9.0 | 0.0 | 1.0 | 0.0 | #VALUE! | #VALUE! | #VALUE! | #VALUE! | #VALUE! | #VALUE!
 |  |  |  |  |  |  |  |  |  |  |  |  |  |  | 29 | 1160 | -2.6 | -2.7 | -2.1 | -2.1 | 0.8 | 5.4 | 3.4 | -2.1 | -2.3 | -1.8 | #VALUE! | #VALUE! | #VALUE! | #VALUE! | #VALUE! | #VALUE! | 6.4 | 1160 | 0.0 | 0.0 | 0.0 | 0.0 | 3.4 | 15.0 | 8.6 | 0.0 | 0.7 | 0.0 | #VALUE! | #VALUE! | #VALUE! | #VALUE! | #VALUE! | #VALUE!
 |  |  |  |  |  |  |  |  |  |  |  |  |  |  | 29.5 | 1180 | -2.6 | -2.7 | -2.1 | -2.1 | 0.5 | 4.7 | 3.2 | -2.1 | -2.5 | -1.8 | #VALUE! | #VALUE! | #VALUE! | #VALUE! | #VALUE! | #VALUE! | 6.4 | 1180 | 0.0 | 0.0 | 0.0 | 0.0 | 2.9 | 14.0 | 8.2 | 0.0 | 0.3 | 0.0 | #VALUE! | #VALUE! | #VALUE! | #VALUE! | #VALUE! | #VALUE!
 |  |  |  |  |  |  |  |  |  |  |  |  |  |  | 30 | 1200 | -2.6 | -2.7 | -2.1 | -2.1 | 0.2 | 4.0 | 2.9 | -2.1 | -2.7 | -1.8 | #VALUE! | #VALUE! | #VALUE! | #VALUE! | #VALUE! | #VALUE! | 6.4 | 1200 | 0.0 | 0.0 | 0.0 | 0.0 | 2.5 | 12.9 | 7.8 | 0.0 | 0.004490854212 | 0.0 | #VALUE! | #VALUE! | #VALUE! | #VALUE! | #VALUE! | #VALUE!
 |  |  |  |  |  |  |  |  |  |  |  |  |  |  | 30.5 | 1220 | -2.6 | -2.7 | -2.1 | -2.1 | -0.008360064061 | 3.4 | 2.7 | -2.1 | -2.7 | -1.8 | #VALUE! | #VALUE! | #VALUE! | #VALUE! | #VALUE! | #VALUE! | 6.4 | 1220 | 0.0 | 0.0 | 0.0 | 0.0 | 2.0 | 11.8 | 7.5 | 0.0 | 0.0 | 0.0 | #VALUE! | #VALUE! | #VALUE! | #VALUE! | #VALUE! | #VALUE!
 |  |  |  |  |  |  |  |  |  |  |  |  |  |  | 31 | 1240 | -2.6 | -2.7 | -2.1 | -2.1 | -0.3 | 2.8 | 2.4 | -2.1 | -2.7 | -1.8 | #VALUE! | #VALUE! | #VALUE! | #VALUE! | #VALUE! | #VALUE! | 6.4 | 1240 | 0.0 | 0.0 | 0.0 | 0.0 | 1.6 | 10.7 | 7.1 | 0.0 | 0.0 | 0.0 | #VALUE! | #VALUE! | #VALUE! | #VALUE! | #VALUE! | #VALUE!
 |  |  |  |  |  |  |  |  |  |  |  |  |  |  | 31.5 | 1260 | -2.6 | -2.7 | -2.1 | -2.1 | -0.5 | 2.1 | 2.2 | -2.1 | -2.7 | -1.8 | #VALUE! | #VALUE! | #VALUE! | #VALUE! | #VALUE! | #VALUE! | 6.4 | 1260 | 0.0 | 0.0 | 0.0 | 0.0 | 1.2 | 9.6 | 6.7 | 0.0 | 0.0 | 0.0 | #VALUE! | #VALUE! | #VALUE! | #VALUE! | #VALUE! | #VALUE!
 |  |  |  |  |  |  |  |  |  |  |  |  |  |  | 32 | 1280 | -2.6 | -2.7 | -2.1 | -2.1 | -0.7 | 1.6 | 2.0 | -2.1 | -2.7 | -1.8 | #VALUE! | #VALUE! | #VALUE! | #VALUE! | #VALUE! | #VALUE! | 6.4 | 1280 | 0.0 | 0.0 | 0.0 | 0.0 | 0.7 | 8.6 | 6.3 | 0.0 | 0.0 | 0.0 | #VALUE! | #VALUE! | #VALUE! | #VALUE! | #VALUE! | #VALUE!
 |  |  |  |  |  |  |  |  |  |  |  |  |  |  | 32.5 | 1300 | -2.6 | -2.7 | -2.1 | -2.1 | -0.9 | 1.0 | 1.8 | -2.1 | -2.7 | -1.8 | #VALUE! | #VALUE! | #VALUE! | #VALUE! | #VALUE! | #VALUE! | 6.4 | 1300 | 0.0 | 0.0 | 0.0 | 0.0 | 0.3 | 7.5 | 5.9 | 0.0 | 0.0 | 0.0 | #VALUE! | #VALUE! | #VALUE! | #VALUE! | #VALUE! | #VALUE!
 |  |  |  |  |  |  |  |  |  |  |  |  |  |  | 33 | 1320 | -2.6 | -2.7 | -2.1 | -2.1 | -1.1 | 0.4 | 1.5 | -2.1 | -2.7 | -1.8 | #VALUE! | #VALUE! | #VALUE! | #VALUE! | #VALUE! | #VALUE! | 6.4 | 1320 | 0.0 | 0.0 | 0.0 | 0.0 | 0.0 | 6.4 | 5.6 | 0.0 | 0.0 | 0.0 | #VALUE! | #VALUE! | #VALUE! | #VALUE! | #VALUE! | #VALUE!
 |  |  |  |  |  |  |  |  |  |  |  |  |  |  | 33.5 | 1340 | -2.6 | -2.7 | -2.1 | -2.1 | -1.1 | -0.1 | 1.3 | -2.1 | -2.7 | -1.8 | #VALUE! | #VALUE! | #VALUE! | #VALUE! | #VALUE! | #VALUE! | 6.4 | 1340 | 0.0 | 0.0 | 0.0 | 0.0 | 0.0 | 5.4 | 5.2 | 0.0 | 0.0 | 0.0 | #VALUE! | #VALUE! | #VALUE! | #VALUE! | #VALUE! | #VALUE!
 |  |  |  |  |  |  |  |  |  |  |  |  |  |  | 34 | 1360 | -2.6 | -2.7 | -2.1 | -2.1 | -1.1 | -0.7 | 1.1 | -2.1 | -2.7 | -1.8 | #VALUE! | #VALUE! | #VALUE! | #VALUE! | #VALUE! | #VALUE! | 6.4 | 1360 | 0.0 | 0.0 | 0.0 | 0.0 | 0.0 | 4.3 | 4.8 | 0.0 | 0.0 | 0.0 | #VALUE! | #VALUE! | #VALUE! | #VALUE! | #VALUE! | #VALUE!
 |  |  |  |  |  |  |  |  |  |  |  |  |  |  | 34.5 | 1380 | -2.6 | -2.7 | -2.1 | -2.1 | -1.1 | -1.2 | 0.9 | -2.1 | -2.7 | -1.8 | #VALUE! | #VALUE! | #VALUE! | #VALUE! | #VALUE! | #VALUE! | 6.4 | 1380 | 0.0 | 0.0 | 0.0 | 0.0 | 0.0 | 3.2 | 4.5 | 0.0 | 0.0 | 0.0 | #VALUE! | #VALUE! | #VALUE! | #VALUE! | #VALUE! | #VALUE!
 |  |  |  |  |  |  |  |  |  |  |  |  |  |  | 35 | 1400 | -2.6 | -2.7 | -2.1 | -2.1 | -1.1 | -1.7 | 0.7 | -2.1 | -2.7 | -1.8 | #VALUE! | #VALUE! | #VALUE! | #VALUE! | #VALUE! | #VALUE! | 6.4 | 1400 | 0.0 | 0.0 | 0.0 | 0.0 | 0.0 | 2.2 | 4.1 | 0.0 | 0.0 | 0.0 | #VALUE! | #VALUE! | #VALUE! | #VALUE! | #VALUE! | #VALUE!
 |  |  |  |  |  |  |  |  |  |  |  |  |  |  | 35.5 | 1420 | -2.6 | -2.7 | -2.1 | -2.1 | -1.1 | -2.2 | 0.5 | -2.1 | -2.7 | -1.8 | #VALUE! | #VALUE! | #VALUE! | #VALUE! | #VALUE! | #VALUE! | 6.4 | 1420 | 0.0 | 0.0 | 0.0 | 0.0 | 0.0 | 1.1 | 3.7 | 0.0 | 0.0 | 0.0 | #VALUE! | #VALUE! | #VALUE! | #VALUE! | #VALUE! | #VALUE!
 |  |  |  |  |  |  |  |  |  |  |  |  |  |  | 36 | 1440 | -2.6 | -2.7 | -2.1 | -2.1 | -1.1 | -2.6 | 0.4 | -2.1 | -2.7 | -1.8 | #VALUE! | #VALUE! | #VALUE! | #VALUE! | #VALUE! | #VALUE! | 6.4 | 1440 | 0.0 | 0.0 | 0.0 | 0.0 | 0.0 | 0.01768222867 | 3.3 | 0.0 | 0.0 | 0.0 | #VALUE! | #VALUE! | #VALUE! | #VALUE! | #VALUE! | #VALUE!
 |  |  |  |  |  |  |  |  |  |  |  |  |  |  | 36.5 | 1460 | -2.6 | -2.7 | -2.1 | -2.1 | -1.1 | -2.7 | 0.2 | -2.1 | -2.7 | -1.8 | #VALUE! | #VALUE! | #VALUE! | #VALUE! | #VALUE! | #VALUE! | 6.4 | 1460 | 0.0 | 0.0 | 0.0 | 0.0 | 0.0 | 0.0 | 3.0 | 0.0 | 0.0 | 0.0 | #VALUE! | #VALUE! | #VALUE! | #VALUE! | #VALUE! | #VALUE!
 |  |  |  |  |  |  |  |  |  |  |  |  |  |  | 37 | 1480 | -2.6 | -2.7 | -2.1 | -2.1 | -1.1 | -2.7 | 0.009765556046 | -2.1 | -2.7 | -1.8 | #VALUE! | #VALUE! | #VALUE! | #VALUE! | #VALUE! | #VALUE! | 6.4 | 1480 | 0.0 | 0.0 | 0.0 | 0.0 | 0.0 | 0.0 | 2.6 | 0.0 | 0.0 | 0.0 | #VALUE! | #VALUE! | #VALUE! | #VALUE! | #VALUE! | #VALUE!
 |  |  |  |  |  |  |  |  |  |  |  |  |  |  | 37.5 | 1500 | -2.6 | -2.7 | -2.1 | -2.1 | -1.1 | -2.7 | -0.2 | -2.1 | -2.7 | -1.8 | #VALUE! | #VALUE! | #VALUE! | #VALUE! | #VALUE! | #VALUE! | 6.4 | 1500 | 0.0 | 0.0 | 0.0 | 0.0 | 0.0 | 0.0 | 2.2 | 0.0 | 0.0 | 0.0 | #VALUE! | #VALUE! | #VALUE! | #VALUE! | #VALUE! | #VALUE!
 |  |  |  |  |  |  |  |  |  |  |  |  |  |  | 38 | 1520 | -2.6 | -2.7 | -2.1 | -2.1 | -1.1 | -2.7 | -0.3 | -2.1 | -2.7 | -1.8 | #VALUE! | #VALUE! | #VALUE! | #VALUE! | #VALUE! | #VALUE! | 6.4 | 1520 | 0.0 | 0.0 | 0.0 | 0.0 | 0.0 | 0.0 | 1.9 | 0.0 | 0.0 | 0.0 | #VALUE! | #VALUE! | #VALUE! | #VALUE! | #VALUE! | #VALUE!
 |  | x |  |  |  |  |  |  |  |  |  |  |  |  | 38.5 | 1540 | -2.6 | -2.7 | -2.1 | -2.1 | -1.1 | -2.7 | -0.5 | -2.1 | -2.7 | -1.8 | #VALUE! | #VALUE! | #VALUE! | #VALUE! | #VALUE! | #VALUE! | 6.4 | 1540 | 0.0 | 0.0 | 0.0 | 0.0 | 0.0 | 0.0 | 1.5 | 0.0 | 0.0 | 0.0 | #VALUE! | #VALUE! | #VALUE! | #VALUE! | #VALUE! | #VALUE!
 |  |  |  |  |  |  |  |  |  |  |  |  |  |  | 39 | 1560 | -2.6 | -2.7 | -2.1 | -2.1 | -1.1 | -2.7 | -0.6 | -2.1 | -2.7 | -1.8 | #VALUE! | #VALUE! | #VALUE! | #VALUE! | #VALUE! | #VALUE! | 6.4 | 1560 | 0.0 | 0.0 | 0.0 | 0.0 | 0.0 | 0.0 | 1.1 | 0.0 | 0.0 | 0.0 | #VALUE! | #VALUE! | #VALUE! | #VALUE! | #VALUE! | #VALUE!
 |  |  |  |  |  |  |  |  |  |  |  |  |  |  | 39.5 | 1580 | -2.6 | -2.7 | -2.1 | -2.1 | -1.1 | -2.7 | -0.8 | -2.1 | -2.7 | -1.8 | #VALUE! | #VALUE! | #VALUE! | #VALUE! | #VALUE! | #VALUE! | 6.4 | 1580 | 0.0 | 0.0 | 0.0 | 0.0 | 0.0 | 0.0 | 0.7 | 0.0 | 0.0 | 0.0 | #VALUE! | #VALUE! | #VALUE! | #VALUE! | #VALUE! | #VALUE!
 |  |  |  |  |  |  |  |  |  |  |  |  |  |  | 40 | 1600 | -2.6 | -2.7 | -2.1 | -2.1 | -1.1 | -2.7 | -0.9 | -2.1 | -2.7 | -1.8 | #VALUE! | #VALUE! | #VALUE! | #VALUE! | #VALUE! | #VALUE! | 6.4 | 1600 | 0.0 | 0.0 | 0.0 | 0.0 | 0.0 | 0.0 | 0.4 | 0.0 | 0.0 | 0.0 | #VALUE! | #VALUE! | #VALUE! | #VALUE! | #VALUE! | #VALUE!
 |  |  |  |  |  |  |  |  |  |  |  |  |  |  | 40.5 | 1620 | -2.6 | -2.7 | -2.1 | -2.1 | -1.1 | -2.7 | -1.1 | -2.1 | -2.7 | -1.8 | #VALUE! | #VALUE! | #VALUE! | #VALUE! | #VALUE! | #VALUE! | 6.4 | 1620 | 0.0 | 0.0 | 0.0 | 0.0 | 0.0 | 0.0 | 0.006889447678 | 0.0 | 0.0 | 0.0 | #VALUE! | #VALUE! | #VALUE! | #VALUE! | #VALUE! | #VALUE!
 |  |  |  |  |  |  |  |  |  |  |  |  |  |  | 41 | 1640 | -2.6 | -2.7 | -2.1 | -2.1 | -1.1 | -2.7 | -1.1 | -2.1 | -2.7 | -1.8 | #VALUE! | #VALUE! | #VALUE! | #VALUE! | #VALUE! | #VALUE! | 6.4 | 1640 | 0.0 | 0.0 | 0.0 | 0.0 | 0.0 | 0.0 | 0.0 | 0.0 | 0.0 | 0.0 | #VALUE! | #VALUE! | #VALUE! | #VALUE! | #VALUE! | #VALUE!
 |  |  |  |  |  |  |  |  |  |  |  |  |  |  | 41.5 | 1660 | -2.6 | -2.7 | -2.1 | -2.1 | -1.1 | -2.7 | -1.1 | -2.1 | -2.7 | -1.8 | #VALUE! | #VALUE! | #VALUE! | #VALUE! | #VALUE! | #VALUE! | 6.4 | 1660 | 0.0 | 0.0 | 0.0 | 0.0 | 0.0 | 0.0 | 0.0 | 0.0 | 0.0 | 0.0 | #VALUE! | #VALUE! | #VALUE! | #VALUE! | #VALUE! | #VALUE!
 |  |  |  |  |  |  |  |  |  |  |  |  |  |  | 42 | 1680 | -2.6 | -2.7 | -2.1 | -2.1 | -1.1 | -2.7 | -1.1 | -2.1 | -2.7 | -1.8 | #VALUE! | #VALUE! | #VALUE! | #VALUE! | #VALUE! | #VALUE! | 6.4 | 1680 | 0.0 | 0.0 | 0.0 | 0.0 | 0.0 | 0.0 | 0.0 | 0.0 | 0.0 | 0.0 | #VALUE! | #VALUE! | #VALUE! | #VALUE! | #VALUE! | #VALUE!
 |  |  |  |  |  |  |  |  |  |  |  |  |  |  | 42.5 | 1700 | -2.6 | -2.7 | -2.1 | -2.1 | -1.1 | -2.7 | -1.1 | -2.1 | -2.7 | -1.8 | #VALUE! | #VALUE! | #VALUE! | #VALUE! | #VALUE! | #VALUE! | 6.4 | 1700 | 0.0 | 0.0 | 0.0 | 0.0 | 0.0 | 0.0 | 0.0 | 0.0 | 0.0 | 0.0 | #VALUE! | #VALUE! | #VALUE! | #VALUE! | #VALUE! | #VALUE!
 |  |  |  |  |  |  |  |  |  |  |  |  |  |  | 43 | 1720 | -2.6 | -2.7 | -2.1 | -2.1 | -1.1 | -2.7 | -1.1 | -2.1 | -2.7 | -1.8 | #VALUE! | #VALUE! | #VALUE! | #VALUE! | #VALUE! | #VALUE! | 6.4 | 1720 | 0.0 | 0.0 | 0.0 | 0.0 | 0.0 | 0.0 | 0.0 | 0.0 | 0.0 | 0.0 | #VALUE! | #VALUE! | #VALUE! | #VALUE! | #VALUE! | #VALUE!
 |  |  |  |  |  |  |  |  |  |  |  |  |  |  | 43.5 | 1740 | -2.6 | -2.7 | -2.1 | -2.1 | -1.1 | -2.7 | -1.1 | -2.1 | -2.7 | -1.8 | #VALUE! | #VALUE! | #VALUE! | #VALUE! | #VALUE! | #VALUE! | 6.4 | 1740 | 0.0 | 0.0 | 0.0 | 0.0 | 0.0 | 0.0 | 0.0 | 0.0 | 0.0 | 0.0 | #VALUE! | #VALUE! | #VALUE! | #VALUE! | #VALUE! | #VALUE!
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

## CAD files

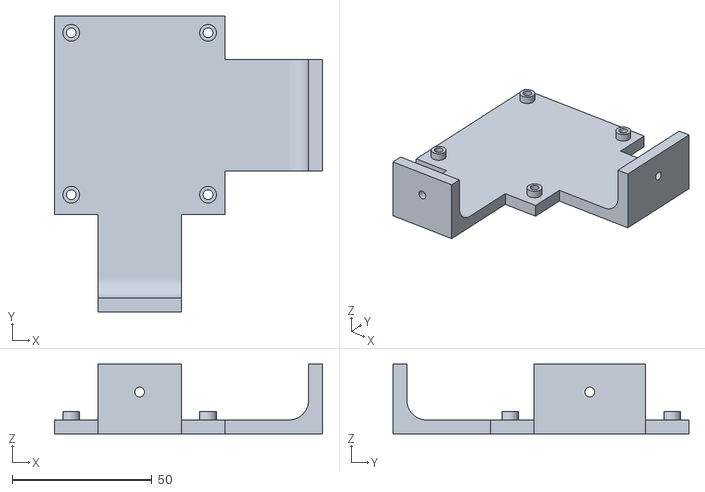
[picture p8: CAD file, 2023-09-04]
STL/Electronics/Mainboard Holder.stl
96.0 x 106.0 x 25.0

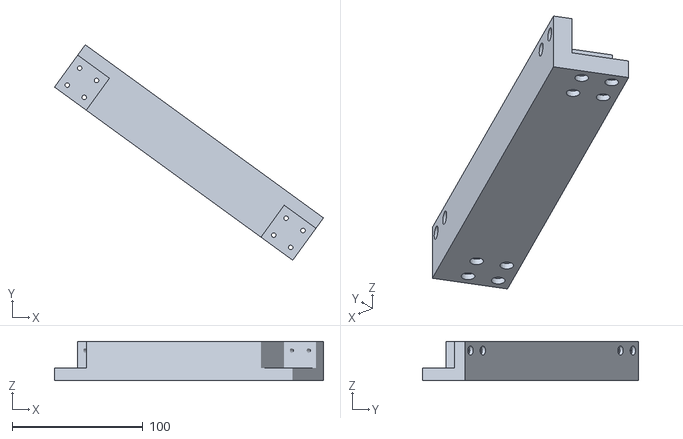
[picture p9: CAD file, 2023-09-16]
STL/Back/Back Connector Right.stl
205.5 x 164.6 x 30.0

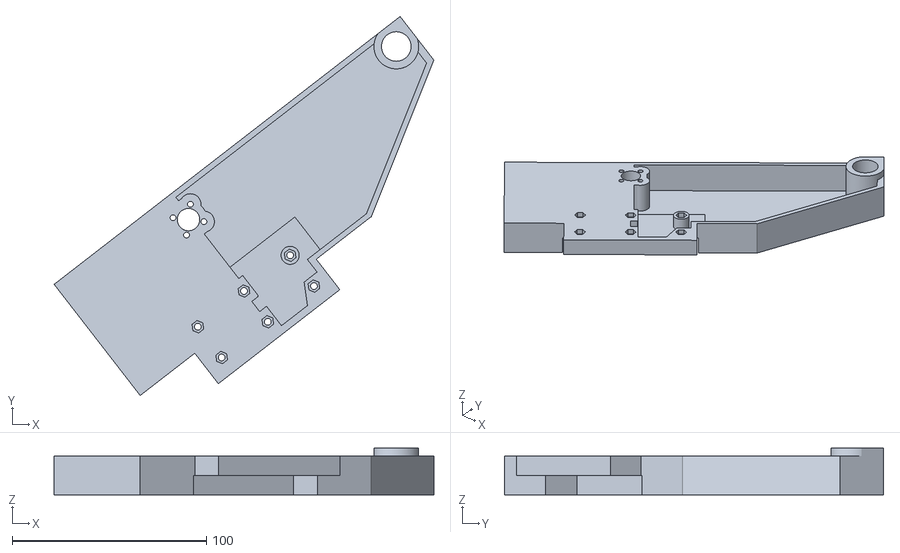
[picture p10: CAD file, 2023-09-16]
STL/Bed/Left.stl
195.3 x 194.9 x 24.0

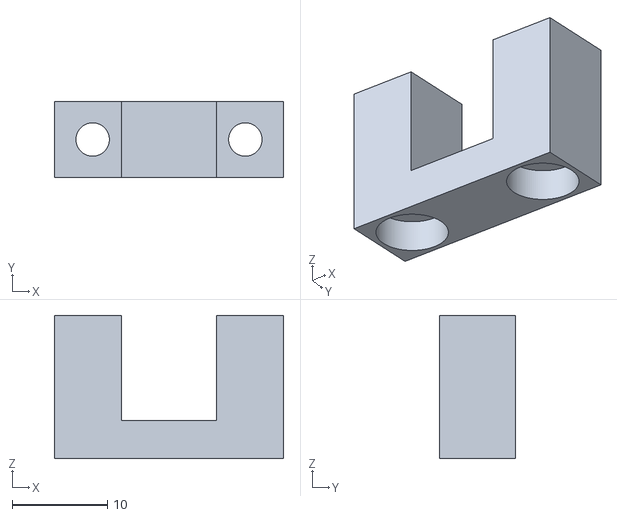
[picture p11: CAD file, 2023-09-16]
STL/Bottom Frame/Cable Guide Clamp.stl
24.0 x 8.00 x 15.0

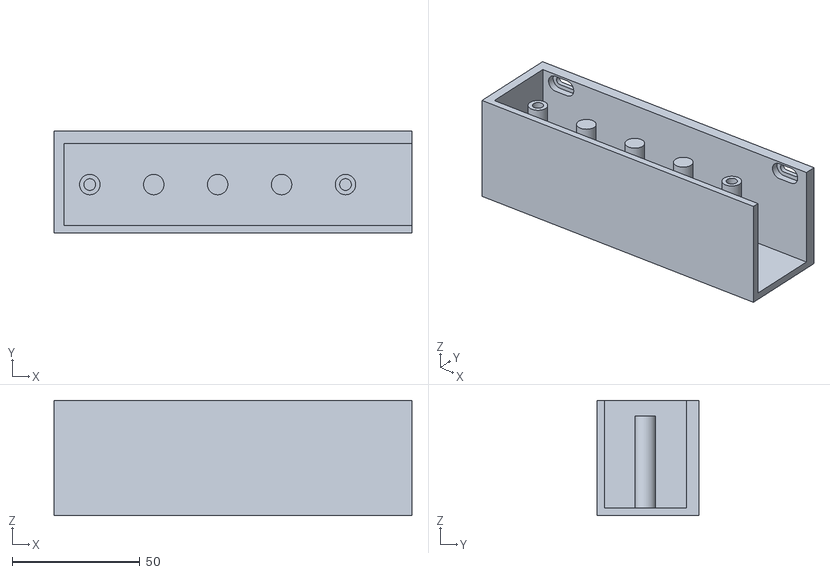
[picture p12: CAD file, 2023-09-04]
STL/Electronics/Cable Holder Frame.stl
140.0 x 40.0 x 45.0

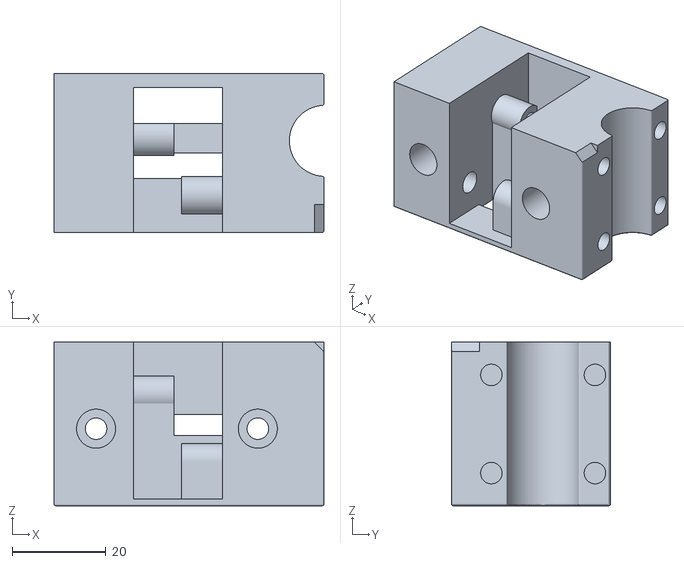
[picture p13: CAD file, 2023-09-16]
STL/Gantry/Right Gantry.stl
57.8 x 34.0 x 35.0

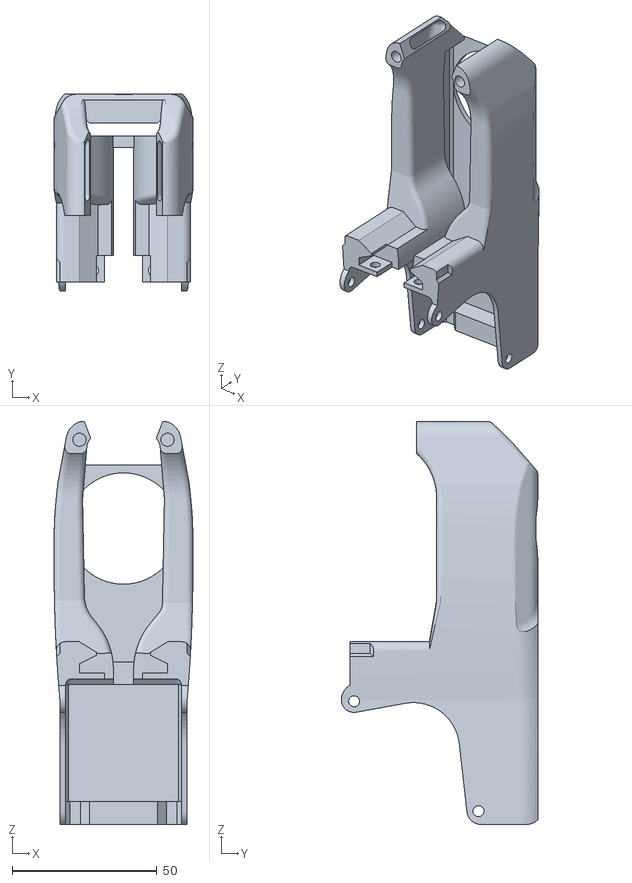
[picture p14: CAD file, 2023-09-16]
STL/Toolhead/CHC Pro/CHC Fanduct.stl
48.0 x 68.0 x 139.4

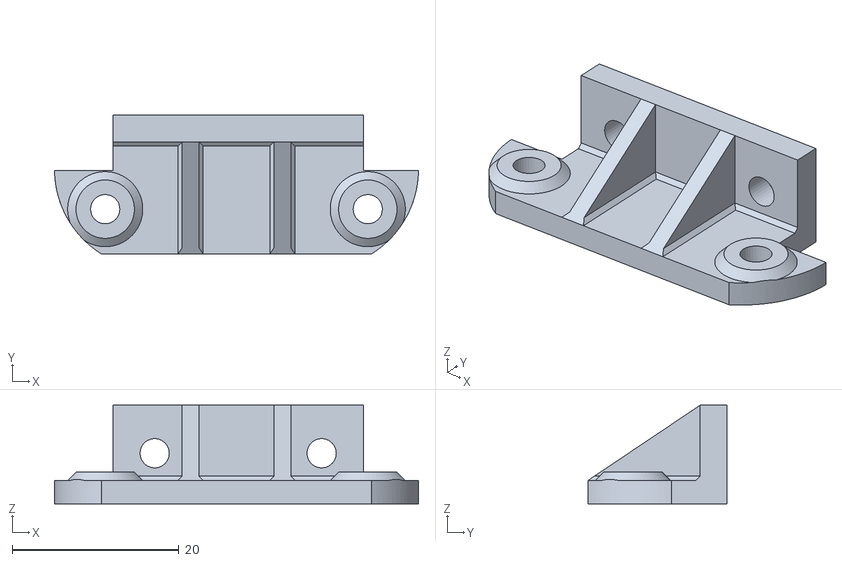
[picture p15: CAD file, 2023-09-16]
STL/Toolhead/Connector Plate.stl
43.6 x 16.6 x 11.8

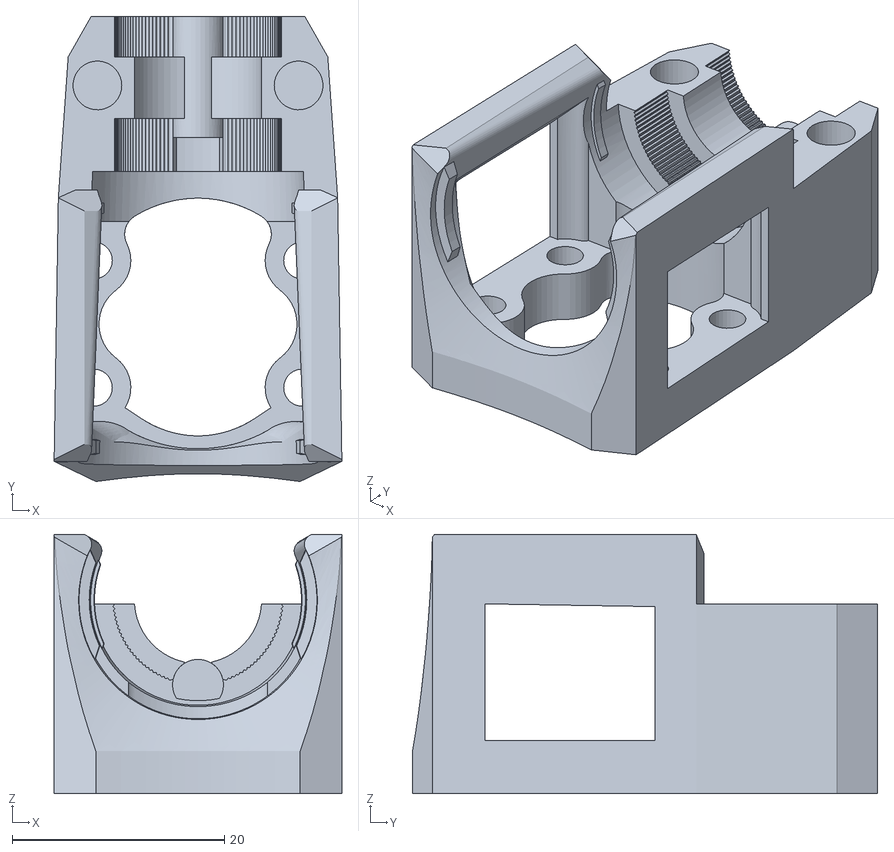
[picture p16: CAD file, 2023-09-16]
STL/Toolhead/Rapido UHF/Hotend Mount.stl
27.1 x 43.8 x 24.4

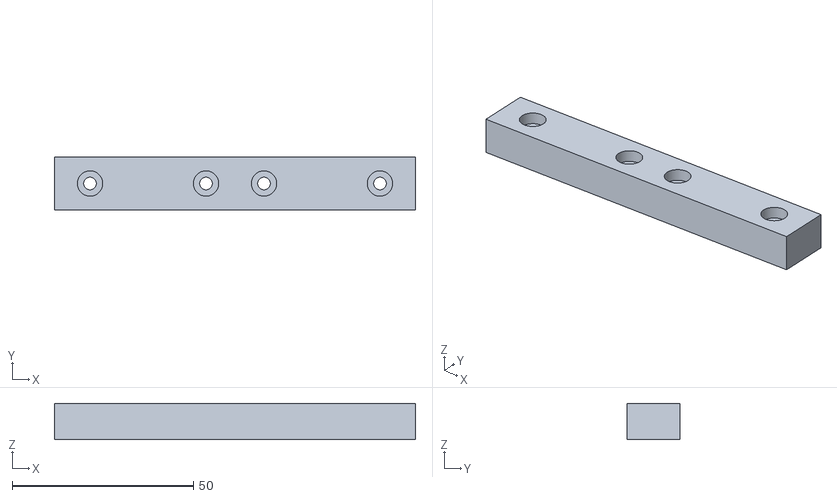
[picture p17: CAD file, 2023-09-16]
STL/Top Frame/Connector Side 2.stl
99.6 x 14.6 x 10.0

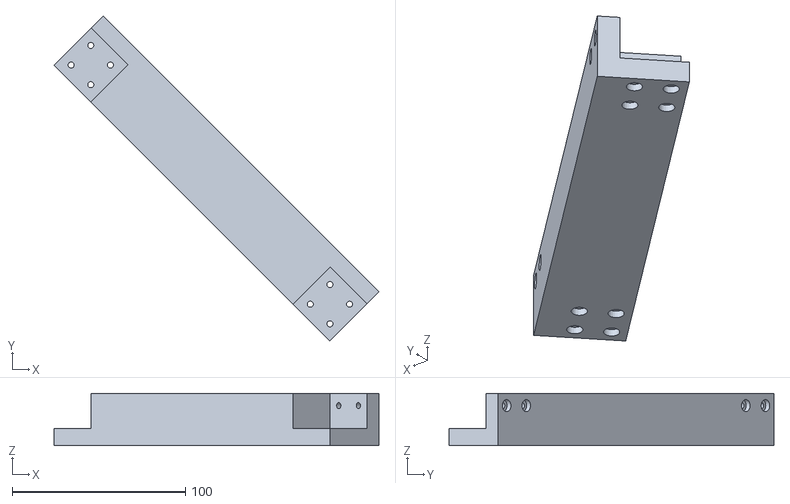
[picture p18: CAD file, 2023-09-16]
STL/Back/Back Connector Left.stl
187.4 x 187.4 x 30.0

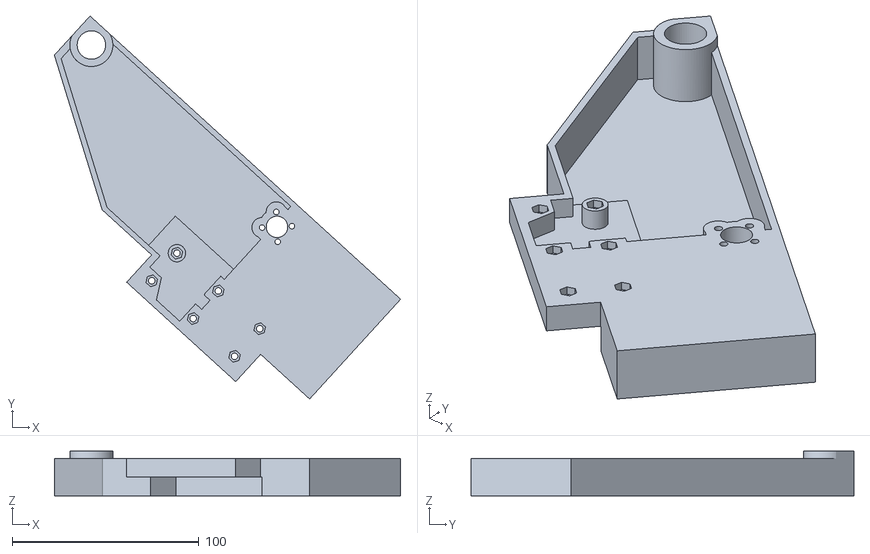
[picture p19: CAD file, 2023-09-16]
STL/Bed/Right.stl
185.4 x 205.0 x 24.0

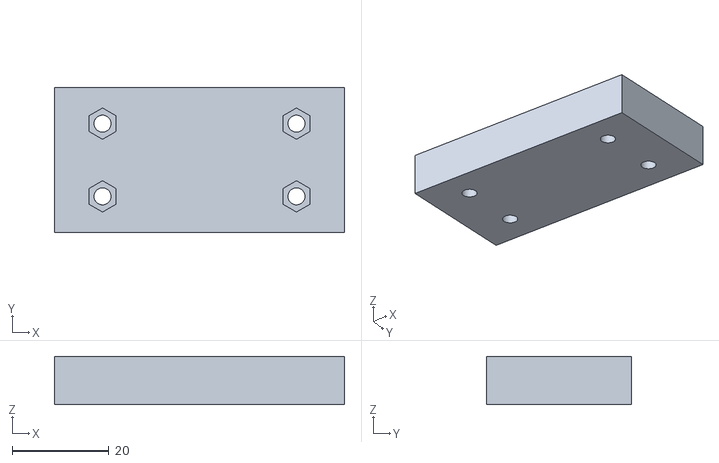
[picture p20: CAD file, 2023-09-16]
STL/Bottom Frame/Frame Connector Front 2.stl
59.8 x 30.0 x 10.0

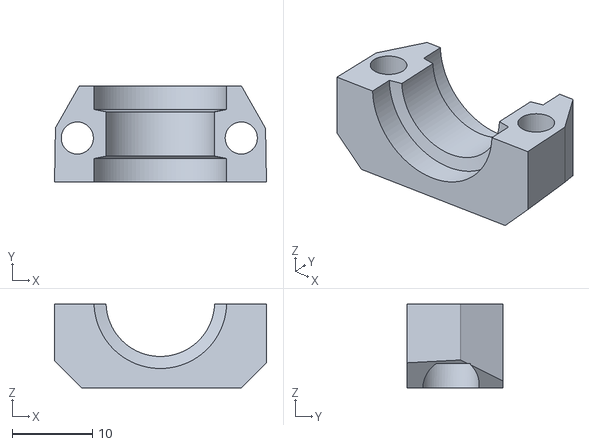
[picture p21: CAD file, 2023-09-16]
STL/Toolhead/CHC Pro/CHC Pro Clamp.stl
26.4 x 12.0 x 10.4

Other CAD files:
STL/Gantry/Left Gantry.stl
STL/Toolhead/Rapido UHF/Hotend Clamp.stl
STL/Toolhead/Rod-Cradle.stl
STL/Top Frame/Rod Holder.stl
STL/Bed/Center.stl
STL/Bottom Frame/Connector Z-Rod.stl
STL/Bottom Frame/Foot Back Left.stl
STL/Bottom Frame/Foot Back Right.stl
STL/Bottom Frame/Foot Front Left.stl
STL/Bottom Frame/Foot Front Right.stl
STL/Bottom Frame/Frame Back Left.stl
STL/Bottom Frame/Frame Back Right.stl
STL/Bottom Frame/Frame Connector Back.stl
STL/Bottom Frame/Frame Connector Front 1.stl
STL/Bottom Frame/Frame Connector Left 1.stl
STL/Bottom Frame/Frame Connector Left 2.stl
STL/Bottom Frame/Frame Connector Right 1.stl
STL/Bottom Frame/Frame Connector Right 2.stl
STL/Bottom Frame/Frame Front Left.stl
STL/Bottom Frame/Frame Front Right.stl
STL/Bottom Frame/Power Cord clamp.stl
STL/Bottom Frame/Z-Coupler.stl
STL/Electronics/Cable Holder Top.stl
STL/Electronics/Spacer 15mm.stl
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

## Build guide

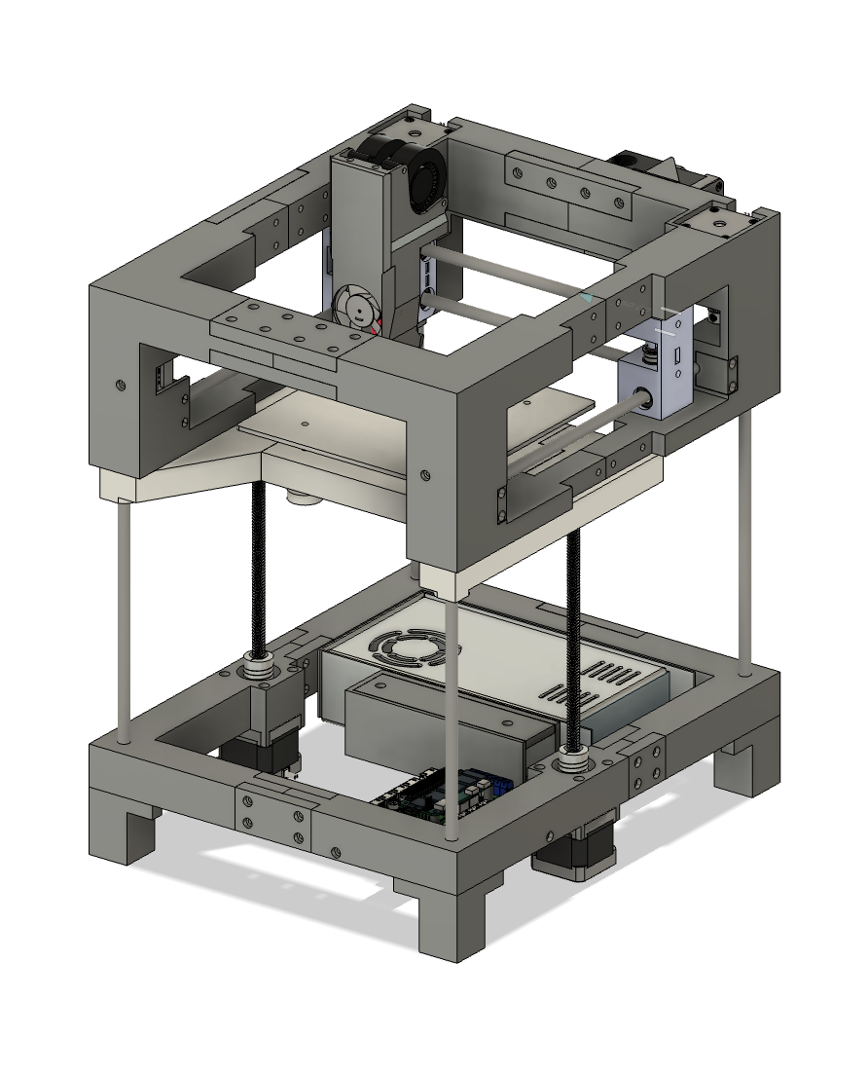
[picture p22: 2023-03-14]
Build_Photos/The 100 Construction.png

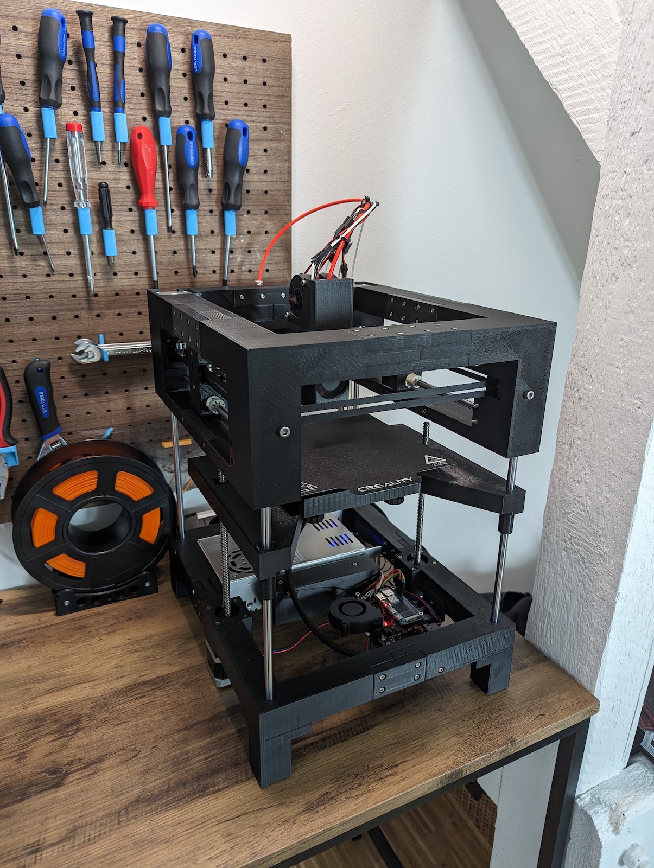
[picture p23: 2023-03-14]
Build_Photos/The 100 Build.jpg

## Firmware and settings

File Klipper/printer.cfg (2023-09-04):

[include fluidd.cfg]
[virtual_sdcard]
path: /home/klipper/printer_data/gcodes
on_error_gcode: CANCEL_PRINT

#####################################################################
#      General Settings
#####################################################################

[mcu]
serial: /dev/ttyS3
restart_method: command

[printer]
kinematics: corexy
max_velocity: 1000
max_accel: 160000
max_z_velocity: 50
max_z_accel: 1000
max_accel_to_decel: 100000
square_corner_velocity: 18.0

[force_move]
enable_force_move: true

[respond]
default_type: echo
default_prefix:

#####################################################################
#      X/Y/Z Stepper Settings
#####################################################################

[stepper_x]
step_pin: gpio11
dir_pin: !gpio10
enable_pin: !gpio12
rotation_distance: 40
microsteps: 16
endstop_pin: tmc2209_stepper_x:virtual_endstop
position_min: -1
position_endstop: -1
position_max: 157
homing_speed: 50
homing_retract_dist: 0

[tmc2209 stepper_x]
uart_pin: gpio9
tx_pin: gpio8
uart_address: 0
run_current: 1.0
stealthchop_threshold: 0
diag_pin: ^gpio4
driver_SGTHRS: 90
interpolate: true

[stepper_y]
step_pin: gpio6
dir_pin: !gpio5
enable_pin: !gpio7
microsteps: 16
rotation_distance: 40
#endstop_pin: ^gpio3
endstop_pin: tmc2209_stepper_y:virtual_endstop
homing_retract_dist: 0
position_min: 0
position_endstop: 174
position_max: 174
homing_speed: 50
homing_positive_dir: true

[tmc2209 stepper_y]
uart_pin: gpio9
tx_pin: gpio8
uart_address: 2
run_current: 1.0
stealthchop_threshold: 0
diag_pin: ^gpio3
driver_SGTHRS: 90
interpolate: true

[stepper_z]
step_pin: gpio19
dir_pin: !gpio28
enable_pin: !gpio2
microsteps: 32
rotation_distance: 8
# endstop_pin: ^gpio25
#position_endstop: -4.3
endstop_pin: tmc2209_stepper_z:virtual_endstop
position_min: -6
position_max: 156
homing_speed: 4

[tmc2209 stepper_z]
uart_pin: gpio9
tx_pin: gpio8
uart_address: 1
run_current: 0.8
diag_pin: ^gpio25
driver_SGTHRS: 50
stealthchop_threshold: 999999

#####################################################################
#      Extruder Settings
#####################################################################

[extruder]
step_pin: gpio14
dir_pin: !gpio13
enable_pin: !gpio15
microsteps: 16
rotation_distance: 23.153
gear_ratio: 50:17
#gear_ratio: 80:20
full_steps_per_rotation: 200
nozzle_diameter: 0.4
filament_diameter: 1.75
heater_pin: gpio23
#sensor_type: EPCOS 100K B57560G104F
sensor_type: ATC Semitec 104NT-4-R025H42G
sensor_pin: gpio27
#control: pid
#pid_Kp: 22.2
#pid_Ki: 1.08
#pid_Kd: 114
min_temp: 0
max_temp: 300
max_extrude_cross_section:2
pressure_advance: 0.4
pressure_advance_smooth_time: 0.060
max_extrude_only_distance: 500
max_extrude_only_velocity: 240
max_extrude_only_accel: 4000
instantaneous_corner_velocity: 20

[tmc2209 extruder]
uart_pin: gpio9
tx_pin: gpio8
uart_address: 3
run_current: 1.0
stealthchop_threshold: 0

#####################################################################
#      Bed Settings
#####################################################################

[heater_bed]
heater_pin: gpio21
sensor_type: EPCOS 100K B57560G104F
sensor_pin: gpio26
#control: pid
#pid_Kp: 54.027
#pid_Ki: 0.770
#pid_Kd: 948.182
min_temp: 0
max_temp: 130

[bed_screws]
screw1: 33, 25
screw2: 128, 25
screw3: 33, 135
screw4: 128, 135

[bed_mesh]
speed: 120
horizontal_move_z: 3
mesh_min: 10, 10
mesh_max: 150,150   
probe_count: 5,5
fade_start: 1
fade_end: 10
fade_target: 0
algorithm: bicubic

#####################################################################
#      Cooling Settings
#####################################################################

[multi_pin part_cooling]
pins: gpio18,gpio20

[fan]
pin: multi_pin:part_cooling

[heater_fan hotend_fan]
pin: gpio17
heater: extruder
heater_temp: 50.0


#####################################################################
#      Sensor Settings
#####################################################################

[temperature_sensor skr_pico]
sensor_type: temperature_mcu
min_temp: 0
max_temp: 100

[temperature_sensor banana_pi]
sensor_type: temperature_host
min_temp: 10
max_temp: 100


#[mcu PIS]
#serial: /dev/serial/by-id/usb-Klipper_rp2040_E66160F4238C3D38-if00
#[mcu USB-ADXL345]
#serial: /dev/serial/by-id/usb-Klipper_stm32f103xe_37FFDA054B48373254491943-if00

#[adxl345]
#cs_pin: USB-ADXL345:PA4
#spi_bus:spi1

#[adxl345]
#cs_pin: PIS:gpio13
#spi_software_sclk_pin: PIS:gpio10
#spi_software_mosi_pin: PIS:gpio11
#spi_software_miso_pin: PIS:gpio12
#axes_map: x,-z,y

#[resonance_tester]
#accel_chip: adxl345 
#probe_points:
#    75,75,20 # an example

#[filament_switch_sensor runout_sensor]
#switch_pin: ^gpio16
#pause_on_runout: True

# [filament_motion_sensor smart_sensor]
# switch_pin: ^gpio16
# detection_length: 2.5

#####################################################################
#      Macros
#####################################################################

[gcode_macro START_PRINT]
gcode:
   {% set BED_TEMP = params.BED|default(60)|int %}
   {% set EXTRUDER_TEMP = params.HOTEND|default(220)|int %}
   CLEAR_PAUSE

   {% if printer.heater_bed.temperature < (BED_TEMP-10) %}
      M140 S{BED_TEMP-10}
   {% endif %}

   G90 ; use absolute coordinates
   G92 E0 ; reset extruder
   
   {% if "xyz" not in printer.toolhead.homed_axes %}
      G28 ; home all axis
   {% endif %}
   G1 ; set units to millimeters

   {% if printer.heater_bed.temperature < (BED_TEMP-10) %}
      M190 S{BED_TEMP-10}
   {% endif %}

   M104 S{EXTRUDER_TEMP}
   M190 S{BED_TEMP}
   M109 S{EXTRUDER_TEMP}
   DRAW_LINE SPEED=1800
   G1 E-2 F900


[gcode_macro CANCEL_PRINT]
rename_existing: BASE_CANCEL_PRINT
gcode:
   M220 S100 ; Reset Speed factor override percentage to default (100%)
   M221 S100 ; Reset Extrude factor override percentage to default (100%)
   G91 ; Set coordinates to relative
   {% if printer.extruder.temperature >= 170 %}
      G1 F1800 E-1 ; Retract filament 3 mm to prevent oozing
   {% endif %}
   ;if all axis are homed, lift the hotend to leave room for hot filament to ooze and to keep it clear of the bed.
   {% if printer.toolhead.homed_axes == "xyz" %}
      G1 F1200 Z20 ; Move Z Axis up 10 mm to allow filament ooze freely
      G90 ; Set coordinates to absolute
      G1 X{ printer.toolhead.axis_minimum.x +10 } Y{ printer.toolhead.axis_maximum.y - 20 } F3600 ; Move Printer Head Out of Way
      ; M84 ; Disable stepper motors - don't so the gantry stays aligned
   {% endif %}
   ;set part fan speed to zero.
   M106 S0
   M104 S{printer.extruder.temperature-20}
   ;bed and hotend are left at the print temps in case I want to restart.
   CLEAR_PAUSE
   BASE_CANCEL_PRINT

[gcode_macro END_PRINT]
gcode:

    # Move nozzle away from print while retracting
    G91 ;releative positioning
    G1 E-2 F2700 ;Retract a bit
    G1 E-2 Z0.2 F2400 ;Retract and raise Z
    G1 X-3 Y-3 F3000 ;Wipe out
    G1 Z10 F1800 ;Raise Z more

    # Turn off bed, extruder, and fan
    M140 S0
    M104 S0
    M106 S0

    G90 ; Absolute Positioning
    G1 X{ printer.toolhead.axis_minimum.x +10 } Y{ printer.toolhead.axis_maximum.y - 20 } F3600 ; Move Printer Head Out of Way

    M84 X Y E ;Disable all steppers but Z

[gcode_macro DRAW_LINE]
gcode:
    {% set SPEED = params.SPEED|default(900)|int %}
    G92 E0 ;Reset Extruder
    G1 Z2.0 F1800 ;Move Z Axis up
    G1 X5.1 Y40 Z0.3 F5000 ;Move to start position
    G1 X5.1 Y140.0 Z0.3 F{SPEED} E15 ;Draw the first line
    G1 X5.4 Y140.0 Z0.3 F{SPEED} ;Move to side a little
    G1 X5.4 Y40 Z0.3 F{SPEED}.0 E30 ;Draw the second line
    G92 E0 ;Reset Extruder
    G1 Z2.0 F3000 ;Move Z Axis up
    G4 P2000

[gcode_macro WAIT_FOR_BED_TEMP]
gcode:
    #Parameters
    {% set s = params.S|float %}

    {% if (s-20) > 0 %}
        TEMPERATURE_WAIT SENSOR=heater_bed MINIMUM={s-20} MAXIMUM={s+1}  ; Wait for bed temp (within 1 degree)
    {% endif %}

[gcode_macro M109]
rename_existing: M99109
gcode:
    #Parameters
    {% set s = params.S|float %}
    
    M104 {% for p in params %}{'%s%s' % (p, params[p])}{% endfor %}  ; Set hotend temp
    {% if s > 0 %}
        TEMPERATURE_WAIT SENSOR=extruder MINIMUM={s-2} MAXIMUM={s+3}   ; Wait for hotend temp (within 3 degree)
    {% endif %}

[gcode_macro M190]
rename_existing: M99190
gcode:
    #Parameters
    {% set s = params.S|float %}

    M140 {% for p in params %}{'%s%s' % (p, params[p])}{% endfor %}   ; Set bed temp
    {% if s > 0 %}
        TEMPERATURE_WAIT SENSOR=heater_bed MINIMUM={s-2} MAXIMUM={s+3}  ; Wait for bed temp (within 3 degree)
    {% endif %}

[gcode_macro G28]
rename_existing: G280
gcode:
  M80
  SET_KINEMATIC_POSITION Z=0
  G90
  G1 Z3 F1200
  SENSORLESS_HOME_X
  SENSORLESS_HOME_Y
  SENSORLESS_HOME_Z

[gcode_macro SENSORLESS_HOME_X]
gcode:
    SENSORLESS_DELAY
    # Home
    G280 X
    # Move away
    G1 X{ printer.toolhead.axis_maximum.x/2 } F6000
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

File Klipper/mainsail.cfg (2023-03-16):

## Mainsail klipper macro definitions
##
## Copyright (C) 2022 Alex Zellner <alexander.zellner@googlemail.com>
##
## This file may be distributed under the terms of the GNU GPLv3 license

## Version 2.0

## add [include mainsail.cfg] to your printer.cfg

## Customization:
## copy the following macro to your printer.cfg (outside of mainsail.cfg)

#[gcode_macro _CLIENT_VARIABLE]
#variable_use_custom_pos  : False ; use custom park coordinates for x,y [True/False] 
#variable_custom_park_x   : 0.0   ; custom x position; value must be within your defined min and max of X
#variable_custom_park_y   : 0.0   ; custom y position; value must be within your defined min and max of Y
#variable_custom_park_dz  : 2.0   ; custom dz value; the value in mm to lift the nozzle when move to park position 
#variable_retract         : 1.0   ; the value to retract while PAUSE
#variable_cancel_retract  : 5.0   ; the value to retract while CANCEL_PRINT
#variable_speed_retract   : 35.0  ; retract speed in mm/s
#variable_unretract       : 1.0   ; the value to unretract while RESUME
#variable_speed_unretract : 35.0  ; unretract speed in mm/s
#variable_speed_hop       : 15.0  ; z move speed in mm/s
#variable_speed_move      : 100.0 ; move speed in mm/s
#variable_park_at_cancel  : False ; allow to move the toolhead to park while execute CANCEL_PRINT [True,False]
## !!! Caution [firmware_retraction] must be defined in the printer.cfg if you set use_fw_retract: True !!!
#variable_use_fw_retract  : False ; use fw_retraction instead of the manual version [True/False] 
#gcode:

## After you uncomment it add your custom values

## You now can use your PAUSE macro direct in your M600 here a short example:

#[gcode_macro M600]
#description: Filament change
#gcode: PAUSE X=10 Y=10 Z_MIN=50

## That will park your head front left with a minimum hight of 50mm above the bed. If your head
## is already above 50mm it will use only the z_hop specified with dz.

[virtual_sdcard]
path: ~/printer_data/gcodes
on_error_gcode: CANCEL_PRINT

[pause_resume]

[display_status]

[gcode_macro CANCEL_PRINT]
description: Cancel the actual running print
rename_existing: CANCEL_PRINT_BASE
gcode:
  ##### get user parameters or use default #####
  {% set allow_park = False if printer['gcode_macro _CLIENT_VARIABLE'] is not defined
                 else False if printer['gcode_macro _CLIENT_VARIABLE'].park_at_cancel is not defined
                 else True  if printer['gcode_macro _CLIENT_VARIABLE'].park_at_cancel|lower == 'true' 
                 else False %}
  {% set retract      = 5.0  if not macro_found else client.cancel_retract|default(5.0)|abs %}
  {% set sp_retract   = 2100 if not macro_found else client.speed_retract|default(35) * 60 %}
  ##### end of definitions #####
  {% if not printer.pause_resume.is_paused and allow_park %} _TOOLHEAD_PARK_PAUSE_CANCEL {% endif %}
  {% if printer.extruder.can_extrude %}
    M83
    G1 E-{retract} F{sp_retract}
    {% if printer.gcode_move.absolute_extrude %} M82 {% endif %}
  {% else %}
    {action_respond_info("Extruder not hot enough")}
  {% endif %}
  TURN_OFF_HEATERS
  M106 S0
  CANCEL_PRINT_BASE

[gcode_macro PAUSE]
description: Pause the actual running print
rename_existing: PAUSE_BASE
gcode:
  PAUSE_BASE
  _TOOLHEAD_PARK_PAUSE_CANCEL {rawparams}

[gcode_macro RESUME]
description: Resume the actual running print
rename_existing: RESUME_BASE
gcode:
  ##### get user parameters or use default #####
  {% set macro_found = True if printer['gcode_macro _CLIENT_VARIABLE'] is defined else False %}
  {% set client = printer['gcode_macro _CLIENT_VARIABLE'] %}
  {% set velocity = printer.configfile.settings.pause_resume.recover_velocity %}
  {% set use_fw_retract = False if not macro_found
                     else False if client.use_fw_retract is not defined
                     else True  if client.use_fw_retract|lower == 'true' and printer.firmware_retraction is defined
                     else False %} 
  {% set unretract      = 1.0  if not macro_found else client.unretract|default(1.0)|abs %}
  {% set sp_unretract   = 2100 if not macro_found else client.speed_unretract|default(35) * 60 %}
  {% set sp_move        = velocity if not macro_found else client.speed_move|default(velocity) %}
  ##### end of definitions #####
  {% if printer.extruder.can_extrude %}
    {% if use_fw_retract %}
      G11
    {% else %}
      M83
      G1 E{unretract} F{sp_unretract}
      {% if printer.gcode_move.absolute_extrude %} M82 {% endif %}
    {% endif %}
  {% else %}
    {action_respond_info("Extruder not hot enough %s" % use_fw_retract)}
  {% endif %}  
  RESUME_BASE VELOCITY={params.VELOCITY|default(sp_move)}  

[gcode_macro _TOOLHEAD_PARK_PAUSE_CANCEL]
description: Helper: park toolhead used in PAUSE and CANCEL_PRINT
gcode:
  ##### get user parameters or use default #####
  {% set macro_found = True if printer['gcode_macro _CLIENT_VARIABLE'] is defined else False %}
  {% set client = printer['gcode_macro _CLIENT_VARIABLE'] %}
  {% set velocity = printer.configfile.settings.pause_resume.recover_velocity %}
  {% set use_custom     = False if not macro_found
                     else False if client.use_custom_pos is not defined
                     else True  if client.use_custom_pos|lower == 'true' 
                     else False %}
  {% set custom_park_x  = 0.0 if not macro_found else client.custom_park_x|default(0.0) %}
  {% set custom_park_y  = 0.0 if not macro_found else client.custom_park_y|default(0.0) %}
  {% set park_dz        = 2.0 if not macro_found else client.custom_park_dz|default(2.0)|abs %}
  {% set use_fw_retract = False if not macro_found
                     else False if client.use_fw_retract is not defined
                     else True  if client.use_fw_retract|lower == 'true' and printer.firmware_retraction is defined
                     else False %}
  {% set retract      = 1.0  if not macro_found else client.retract|default(1.0)|abs %}
  {% set sp_retract   = 2100 if not macro_found else client.speed_retract|default(35) * 60 %}
  {% set sp_hop       = 900  if not macro_found else client.speed_hop|default(15) * 60 %}
  {% set sp_move      = velocity * 60 if not macro_found else client.speed_move|default(velocity) * 60 %}
  ##### get config and toolhead values #####
  {% set act = printer.toolhead.position %}
  {% set max = printer.toolhead.axis_maximum %}
  {% set cone = printer.toolhead.cone_start_z|default(max.z) %} ; hight as long the toolhead can reach max and min of an delta
  {% set round_bed = True if printer.configfile.settings.printer.kinematics is in ['delta','polar','rotary_delta','winch'] 
                else False %}
  ##### define park position #####
  {% set z_min = params.Z_MIN|default(0)|float %}
  {% set z_park = [[(act.z + park_dz), z_min]|max, max.z]|min %}
  {% set x_park = params.X       if params.X is defined
             else custom_park_x  if use_custom
             else 0.0            if round_bed 
             else (max.x - 5.0) %}
  {% set y_park = params.Y       if params.Y is defined
             else custom_park_y  if use_custom
             else (max.y - 5.0)  if round_bed and z_park < cone
             else 0.0            if round_bed
             else (max.y - 5.0) %}
  ##### end of definitions #####
  {% if printer.extruder.can_extrude %}
    {% if use_fw_retract %}
      G10
    {% else %}
      M83
      G1 E-{retract} F{sp_retract}
      {% if printer.gcode_move.absolute_extrude %} M82 {% endif %}
    {% endif %}
  {% else %}
    {action_respond_info("Extruder not hot enough")}
  {% endif %}
  {% if "xyz" in printer.toolhead.homed_axes %}
    G90
    G1 Z{z_park} F{sp_hop}
    G1 X{x_park} Y{y_park} F{sp_move}
    {% if not printer.gcode_move.absolute_coordinates %} G91 {% endif %}
  {% else %}
    {action_respond_info("Printer not homed")}
  {% endif %}

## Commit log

2023-03-14 added all stl files
    [BeltFastener.stl, Bottom 1.stl, Bottom 2.stl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]
2023-03-16 Added print settings for stl files
2023-03-16 added klipper config
    [mainsail.cfg, printer.cfg]
2023-03-18 Updated BOM Link
2023-03-19 Added Cura Configuration Guide & Cura Printer profiles
2023-03-25 updated BOM
2023-03-26 removed BOM.pdf. Use Spreadsheet linked in the README
2023-07-30 added motor sim database
    [motor_torque_sim_v9_database_updated.xlsm]
2023-09-04 release v1.1
    [Back-Left.stl, Back-Right.stl, Belt Fastener.stl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]
2023-09-04 updated klipper.cfg
    [printer.cfg]
2023-09-04 added fluid.cfg
    [fluidd.cfg]
2023-09-04 added back parts
    [Back Connector Left.stl, Back Connector Right.stl]
2023-09-05 Update link to printables for v1.1
2023-09-07 added Z-Coupler STL
    [Z-Coupler.stl]
2023-09-16 updated STL orientation (thx DGP_Maluco)
    [Back Connector Left.stl, Back Connector Right.stl, Back-Left.stl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]
